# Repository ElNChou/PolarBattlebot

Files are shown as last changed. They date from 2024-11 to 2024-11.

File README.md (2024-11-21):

# PinguBot - 2024

### Historia del Battlebot
Los climas helados son muy castigadores. No solo por todas las dificultades que presenta sobrevivir a temperaturas extremas, si no que también por lo gente que aparece por estos lugares sin prepararse. Estas personas son lentamente consumidas por el frío insoportable hasta lo más profundo de su ser, haciéndoles perder el interés por la cosas y la bondad. Esto es algo que Pingu sabe muy bien, pues ha sido víctima de un acto de crueldad solo posible con alguien de frío corazón.

En uno de sus paseos rutinarios con su querida madre, Pingu se alejó demasiado y se perdió por la montaña helada en que se encontraban explorando, pero encontró a un humano extremadamente amable que lo encontró. Sin esperar nada a cambio, este humano lo llevó en brazos hasta llevarlo de vuelta con su admirada guardiana, pero justo antes de que pudieran darle las gracias, este individuo cambió completamente de parecer y arrojó a Pingu al acantilado, enfrente de su madre.

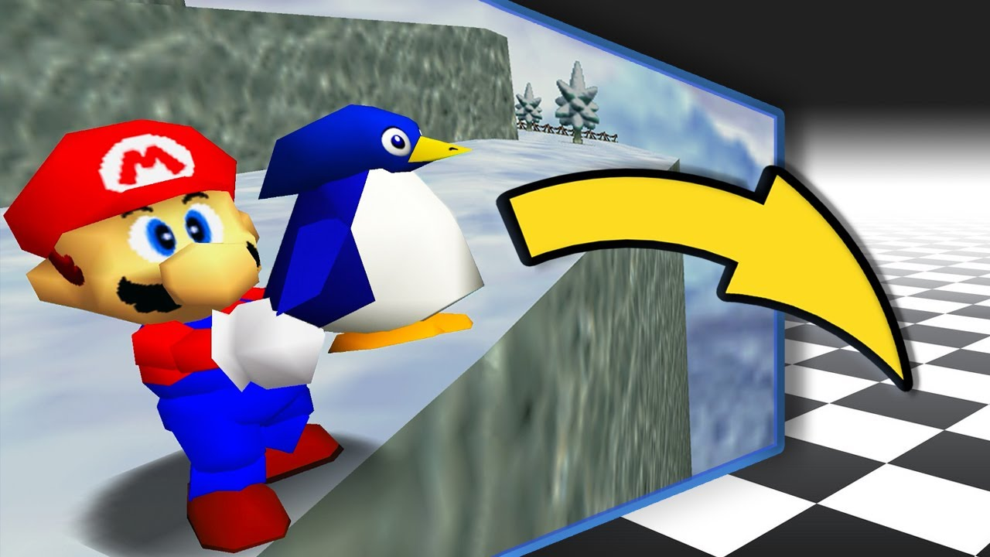
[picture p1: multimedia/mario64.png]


Tras este acto completamente repentino, Pingu cayó mientras escuchaba a lo lejos los ruidos que su furiosa madre hacía, desvaneciéndose lentamente... pero con una caída estratégica logró sobrevivir. Con esto aprendió a nunca más confiar en extraños, pues no se podía creer que alguien fuera capaz hacer algo así.
Tras este suceso, nuestra ave caída decidió nunca más salir de su iglú, y convertirlo en un tanque de guerra que lo protegiese, con el que se adentraría en la sociedad humana buscando a este malhechor.

Su extenuante búsqueda lo trajo a la competencia de battlebots, en donde pondrá a prueba sus habilidades y la resistencia de su querido transporte, con el que tantos viajes ha compartido.
  
¡Afiche del robot!
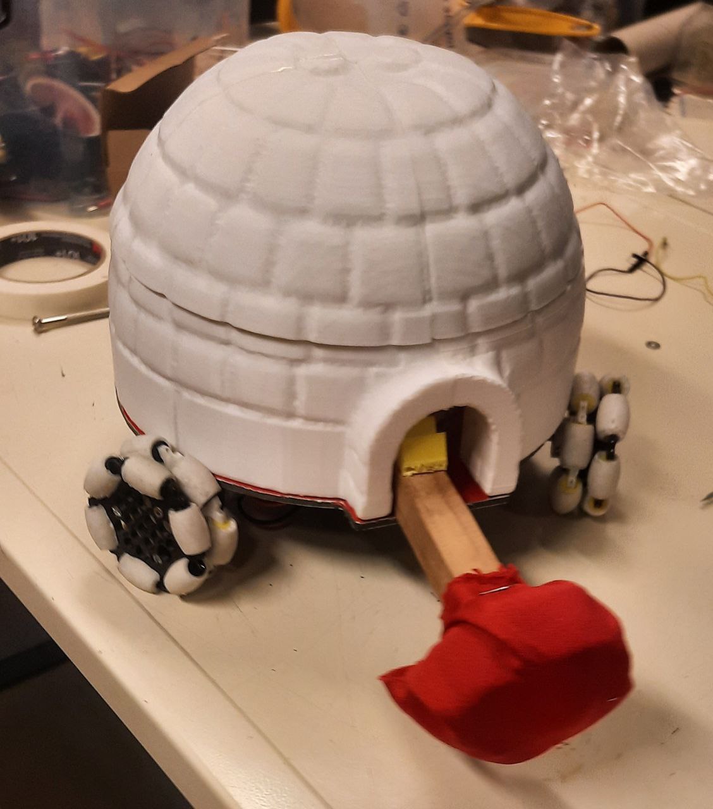
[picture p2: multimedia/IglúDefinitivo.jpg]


## Integrantes
- Camila Cáceres T. -  FCFM 
- Javier Ignacio Azócar -  FCFM 
- Tomás Rajevic P. -  FCFM 

## Descripción del proyecto
  El robot de batalla se comunica a través de wifi, tiene una coraza con forma de iglú y cuenta con 3 ruedas omnidireccionales que permiten un desplazamiento amplio sin necesidad de rotación, además de un arma de resorte que empuja a los rivales al soltarse. Las ruedas, coraza y partes internas del arma fueron impresas en 3D y la base fue procesada en una máquina CNC.
### Estrategia utilizada
  
#### Ofensiva
El arma es un palo que tiene espuma en la punta, unido a un resorte que acumula tensión y se suelta para realizar un empuje análogo a un guante de boxeo.
Debido a problemas técnicos con el motor que usaba para esto (¡resultó estar malo!), se cambió por un servomotor a último momento tal que solo moviera el arma para farmear puntos.

#### Defensiva
La defensa del robot viene dada por su corteza, ya que al ser una semi esfera dificulta recibir golpes directos pues se deflectan ligeramente al no golpearse contra una superficie plana. Además tiene un desplazamiento omnidireccional, el cual facilita aprovechar los ángulos de su coraza y esquivar ataques o reposicionarse sin necesidad de frenarse al rotar.

### Diagrama funcional
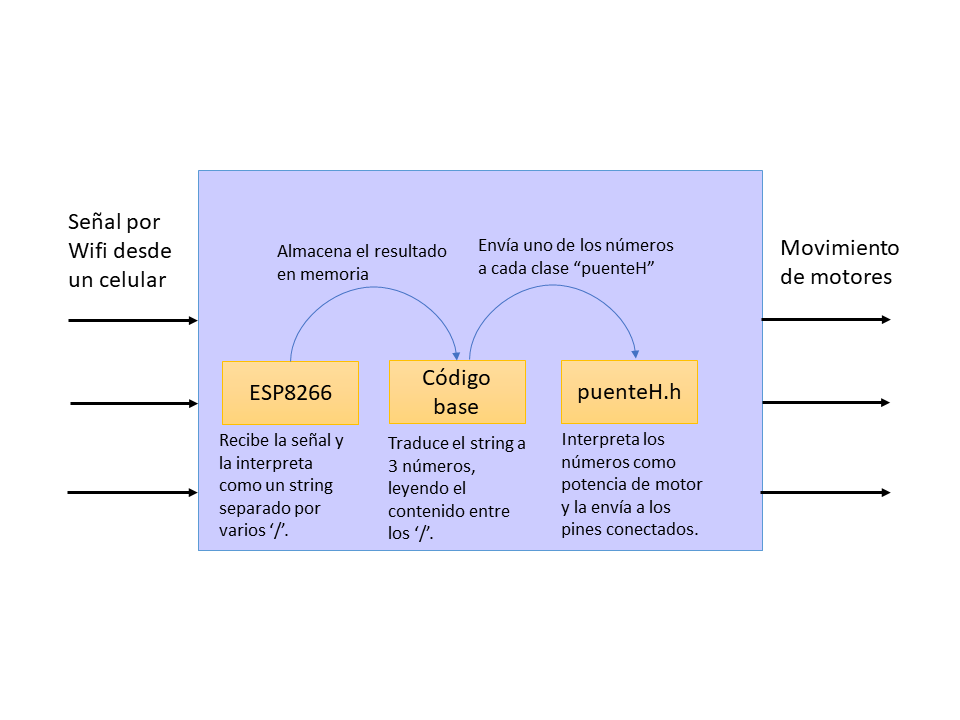
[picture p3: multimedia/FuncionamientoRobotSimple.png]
Robot Ejemplo


## Licencia
<br />Esta obra está bajo una <a rel="license" href="http://creativecommons.org/licenses/by-nc/4.0/">Licencia Creative Commons Atribución-NoComercial 4.0 Internacional</a>.

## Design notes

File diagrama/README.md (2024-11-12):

# Diagrama electromecánico

El arma es muy simple: Solo utiliza un pin digital para mover un motor hacia atrás, tensando así el resorte hasta que la rueda llega al final y se suelta, liberando un golpe sencillo y rápido, para luego volver a cargarse.

¿Pero cómo movemos el motor? No es suficiente con solo aplicarle el pin digital, por lo que compartirá un puenteH con la tercera omniwheel. La idea de esto es que aproveche la energía proporcionada por la batería, pues debe ser capaz de oponerse al resorte.

Para que esto se pueda hacer utilizando un solo pin, se cierra la parte del circuito donde normalmente iría el ENB, en el Pin1B se coloca el que queramos usar para activar el motor y Pin2B estará siempre cerrado, así que lo conectamos a a tierra sacrificando a la vez la flexibilidad de mover el motor en resera, pero para el arma no nos interesa. Gracias a eso, podemos controlar el motor aprovechando la pila de la batería sencillamente, utilizando un solo pin.

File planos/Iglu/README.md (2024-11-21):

# Modelo original que fue modificado
https://www.printables.com/model/204324-igloo-ornament

# MUY IMPORTANTE:
La base del iglú está mal medida y es posible que algunos agujeros no entren en caso de hacerlos con un taladro my pequeño. También es muy posible que si utilizas el arma en su forma predeterminada (un motor DC) debas cortarle algunas de las púas, están hecho más largos de lo normal pues es más fácil cortarlos que imprimir de nuevo.

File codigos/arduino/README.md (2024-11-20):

# Códigos Arduino
El código de este robot tiene dos archivos, el archivo 'puenteH' contiene una clase que nos permite mover un motor solo llamando a 'motor.move(valor)', el cual puede interpretar la dirección del movimiento a partir del signo del número que recibe. Polar.ino es el código principal que permite la conexión a la aplicación y requiere tener "puente.h" en la carpeta del proyecto..

Asegúrate que los pines coincidan con los del programa:

Si te posicionas en la misma dirección en la que mira el iglú, "Right" es el motor conectado a la derecha, "Left" a la izquierda, y "Tail" el que está por detrás (opuesto a la puerta). Los tres pines en cada uno de estos motores van en el orden de "OUT1,OUT2,ENA".

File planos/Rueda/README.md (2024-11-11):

# Molde
Archivos stl los cuales luego pueden ser usados para hacer un roller cubierto de caucho/silicona

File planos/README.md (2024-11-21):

# Archivos de planos incluidos

Aquí se encuentran todos los modelos utilizados para crear el battebot, además de algunos de referencia.

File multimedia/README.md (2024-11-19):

# Archivos multimedia de los battlebots

Se deben subir:
- Fotos de avance (en orden cronológico)

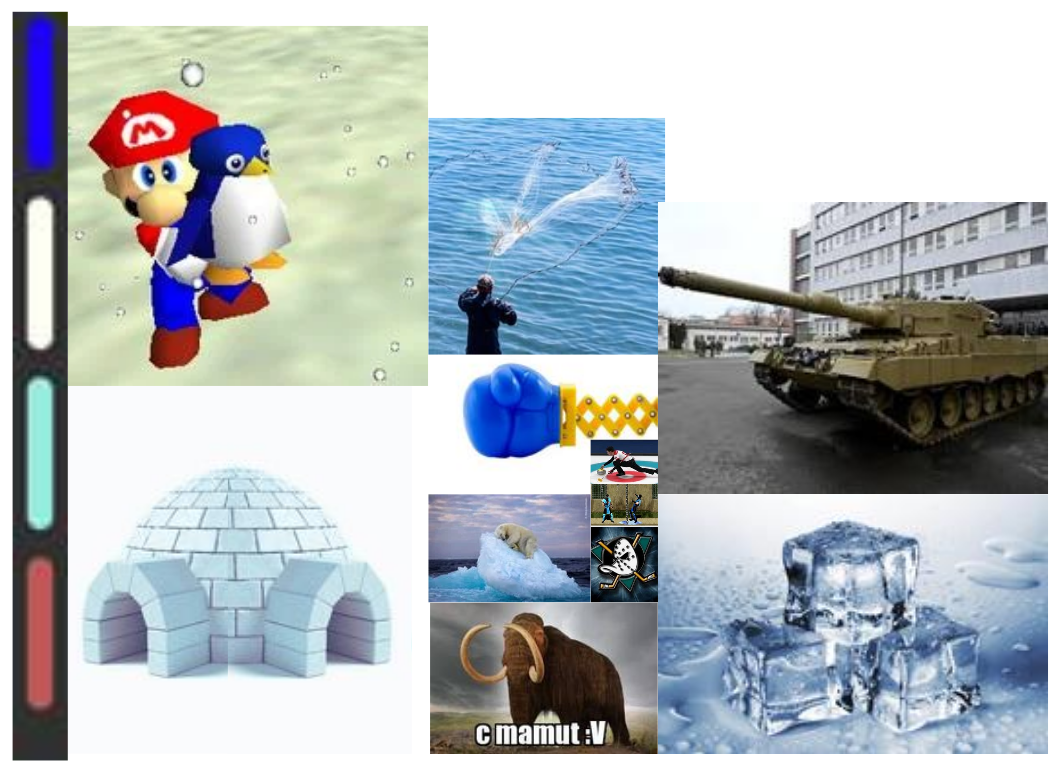
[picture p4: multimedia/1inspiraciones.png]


Imagen

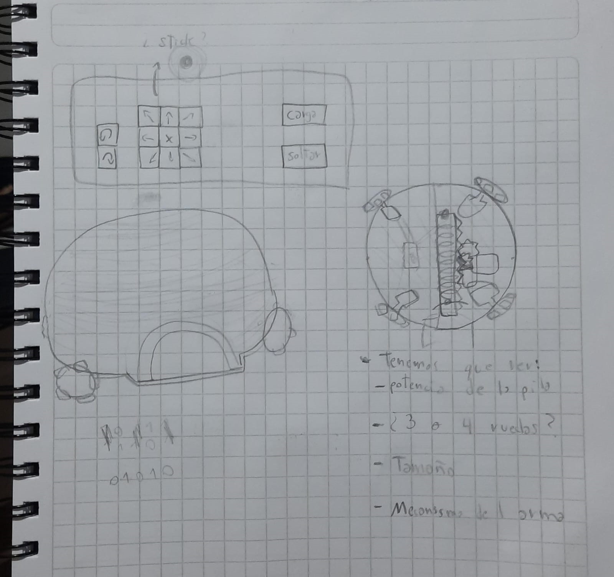
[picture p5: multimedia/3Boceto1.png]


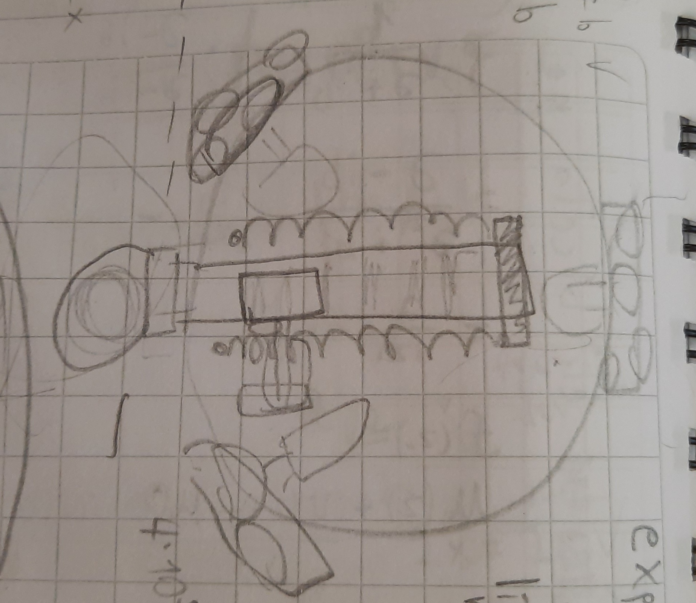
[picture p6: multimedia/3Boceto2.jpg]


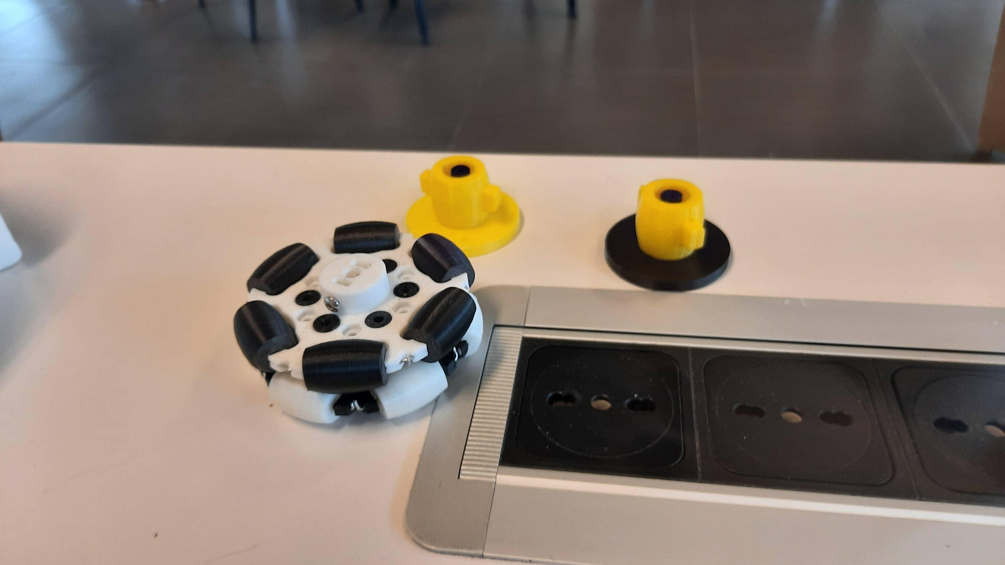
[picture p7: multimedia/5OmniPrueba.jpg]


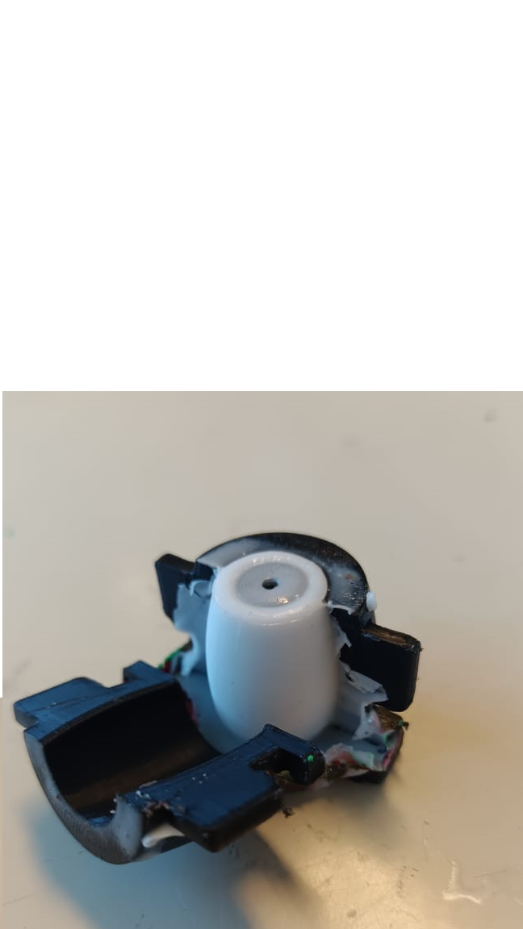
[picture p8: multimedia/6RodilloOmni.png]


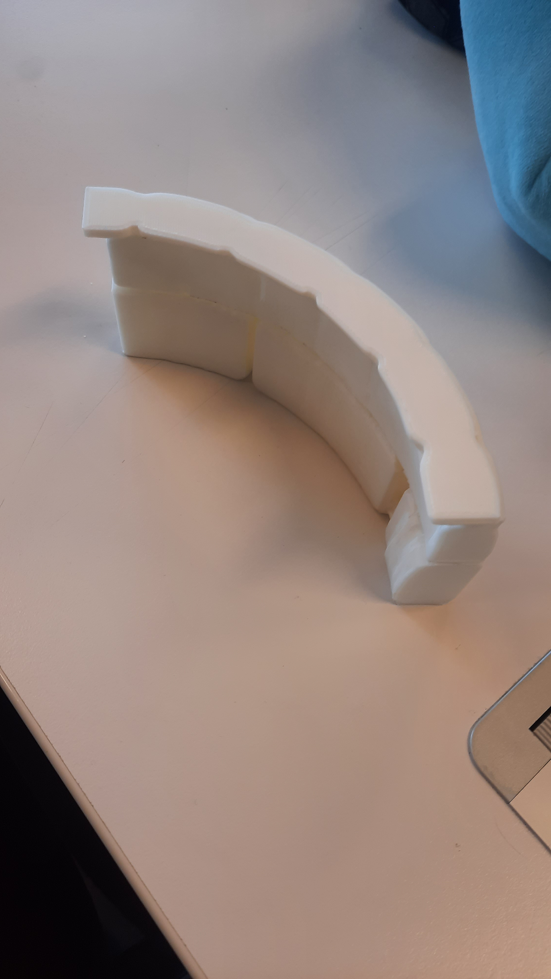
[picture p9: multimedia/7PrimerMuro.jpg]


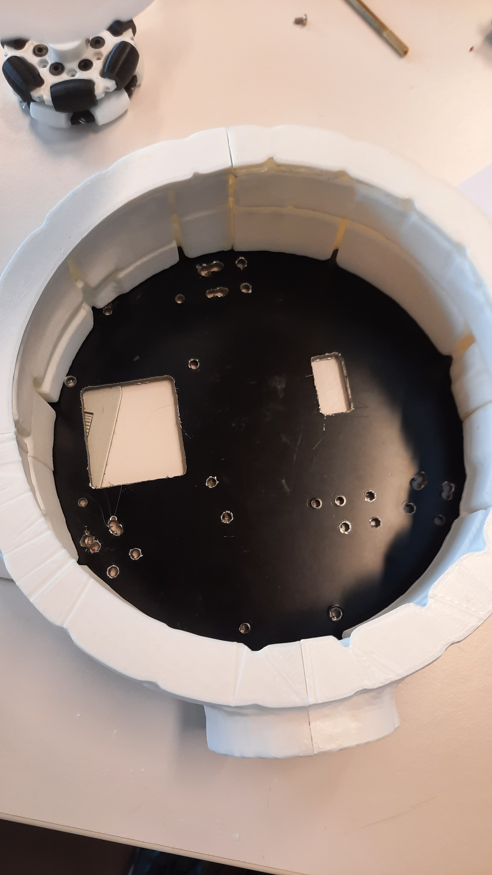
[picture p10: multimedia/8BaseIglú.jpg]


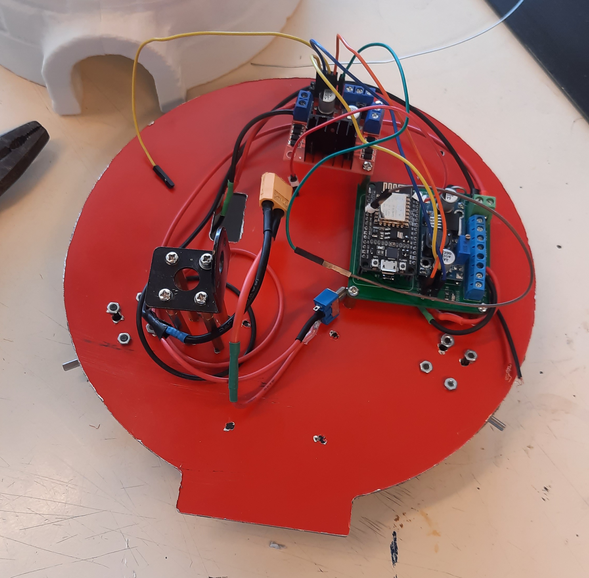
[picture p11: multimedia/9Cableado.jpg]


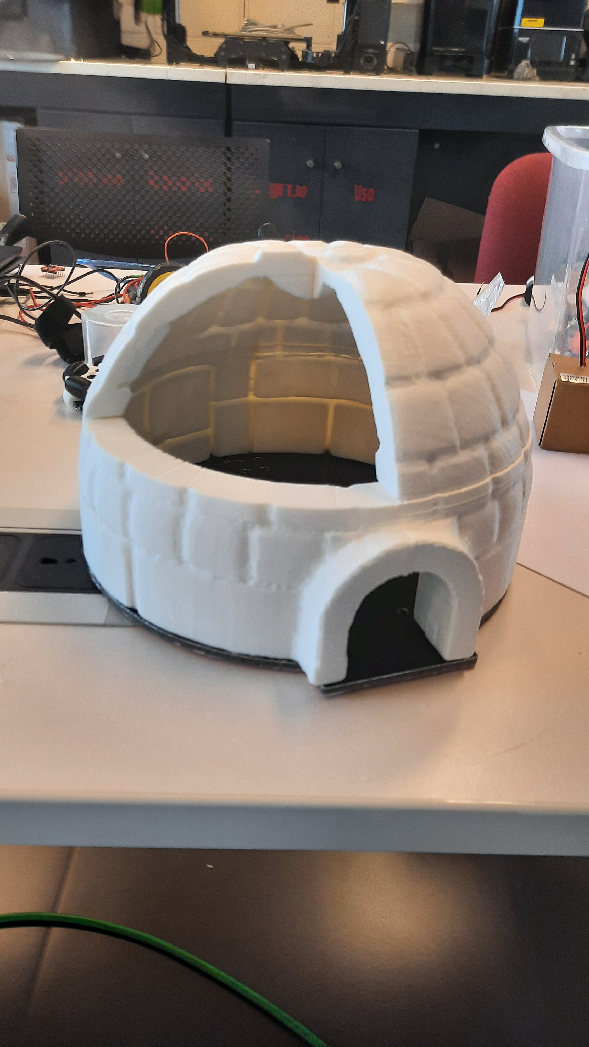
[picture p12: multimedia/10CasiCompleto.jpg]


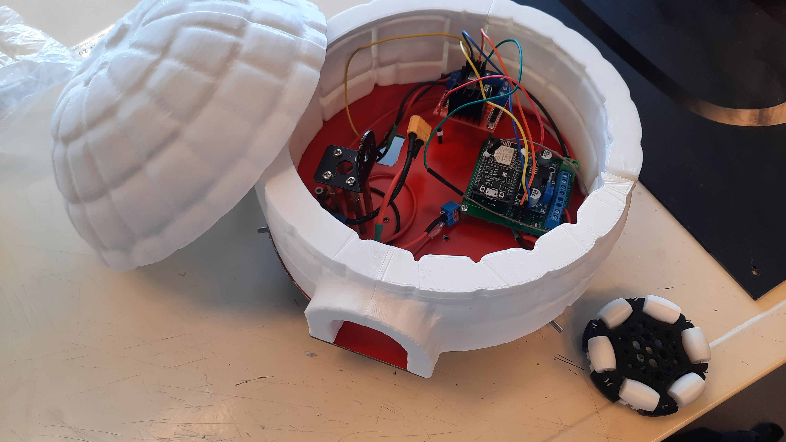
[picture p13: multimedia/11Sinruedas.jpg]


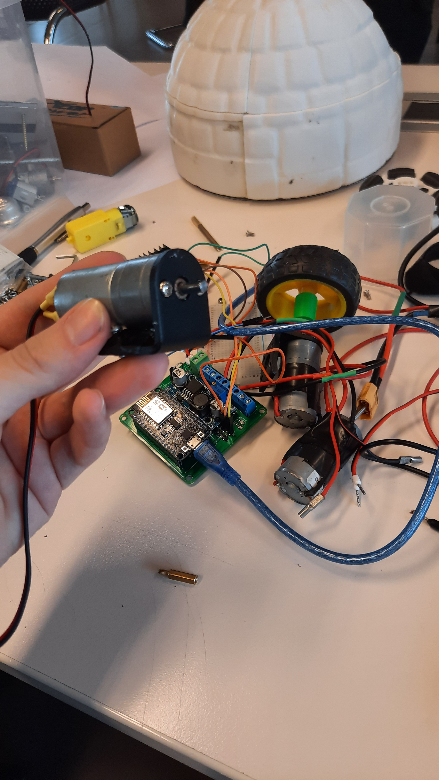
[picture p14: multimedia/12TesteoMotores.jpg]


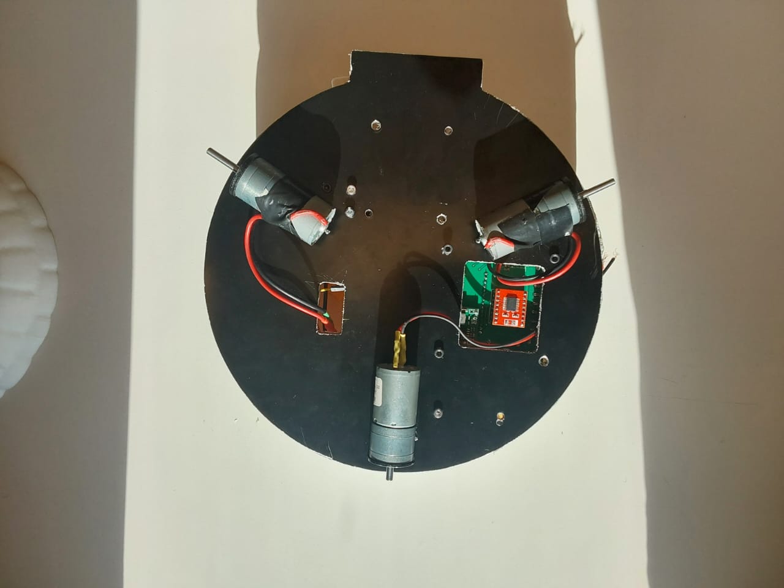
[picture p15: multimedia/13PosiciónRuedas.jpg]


Imagen

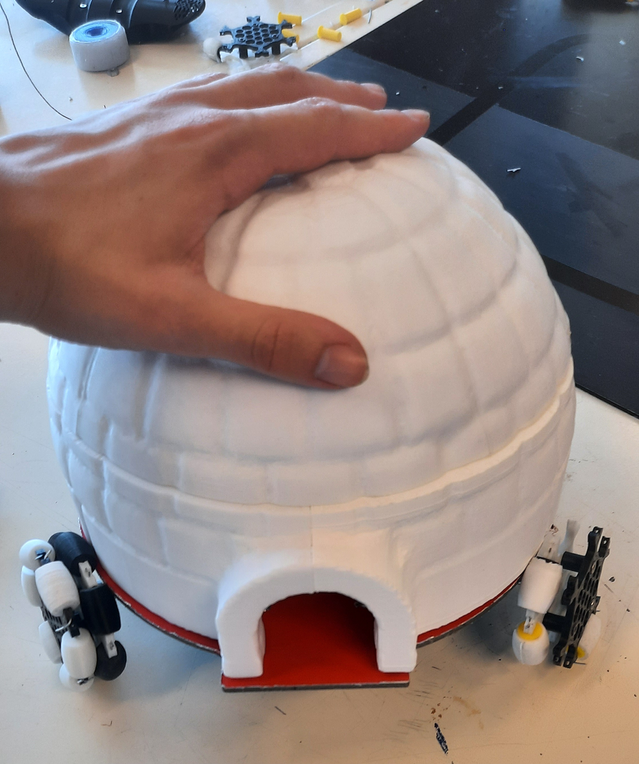
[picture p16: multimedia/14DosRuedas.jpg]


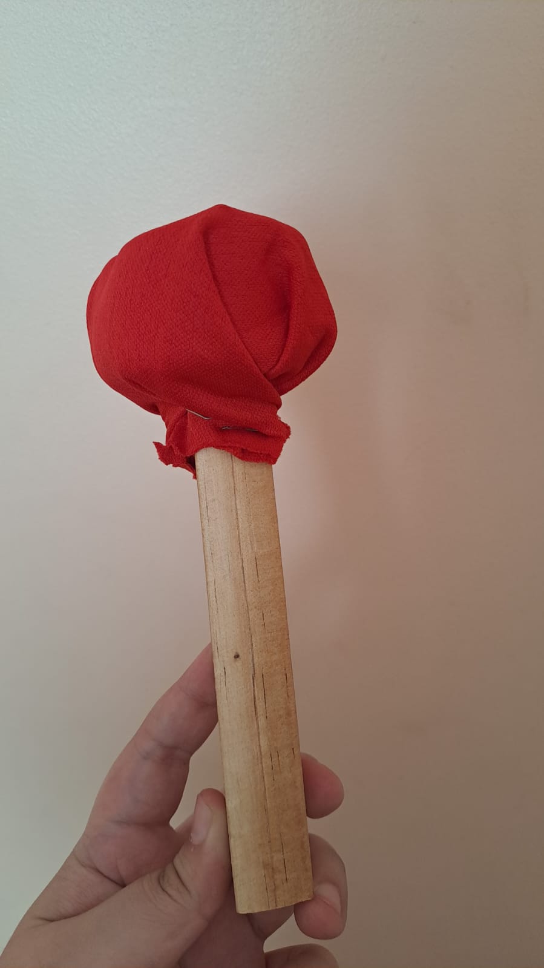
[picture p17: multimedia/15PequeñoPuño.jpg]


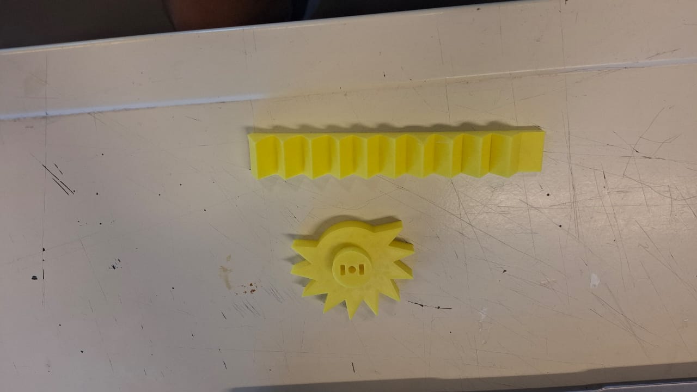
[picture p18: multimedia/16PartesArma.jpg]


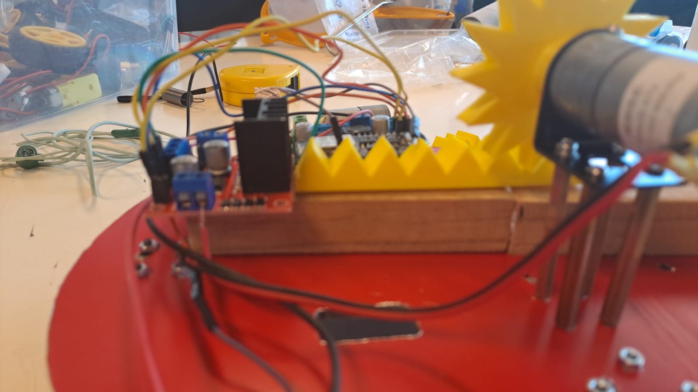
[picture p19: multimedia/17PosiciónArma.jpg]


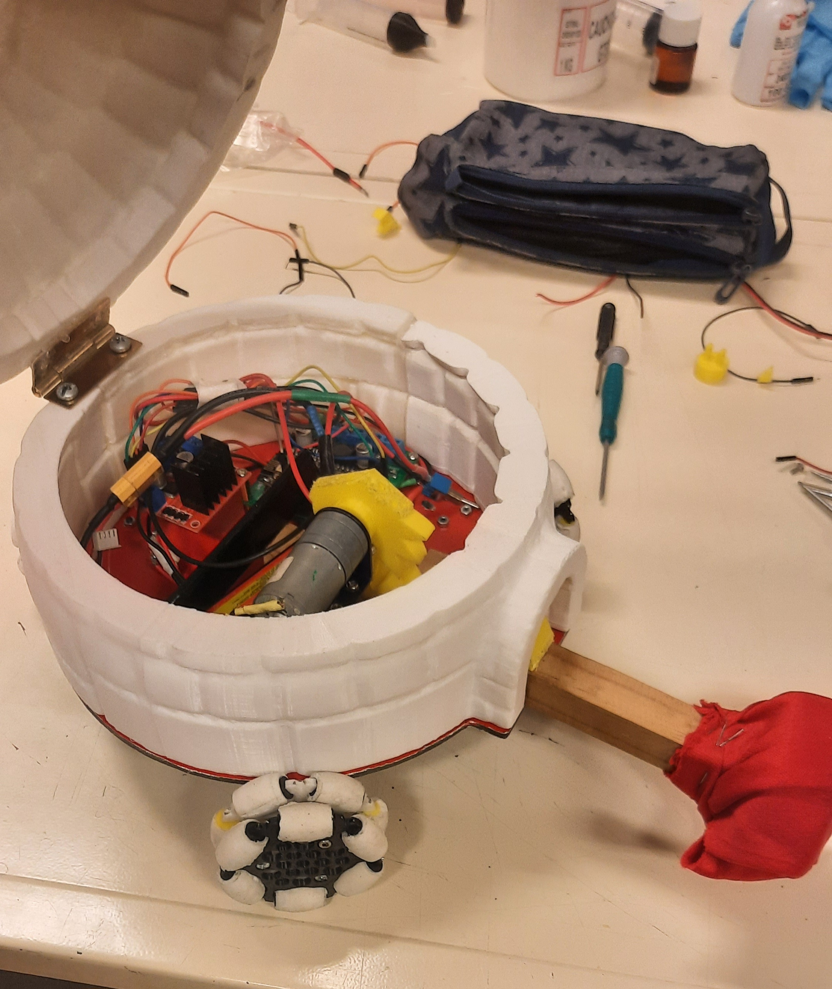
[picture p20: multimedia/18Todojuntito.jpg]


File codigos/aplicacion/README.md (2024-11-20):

# Código de la Aplicación

Aquí se encuentra la aplicación con la que se controla al robot.
Está el instalador apk, una foto del diagrama de bloques y el proyecto de appinventor aia

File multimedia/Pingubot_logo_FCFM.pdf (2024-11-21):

Equipo: Polar
Integrantes: Tomás Rájevic
Javier Azócar
Camila Cáceres
Curso: Módulo Interdisciplinario Battlebots | Nombre de Proyecto: PinguBot
| Descripción: Robot de batalla con ruedas omnidireccionales y un arma que dispara un golpe hacia delante. Está principalmente impreso en 3D, funciona con un ESP8266 y tiene forma de iglú
logos | Fecha: 12-11-2024

### Historia Había una vez, un pingüino que vivía en la cima de una montaña, de la cual fue lanzado al acantilado por un hombre muy malvado. Pingu pudo sobrevivir a la caída, pero desde ese día no confía en el resto, y convirtió su iglú en un tanque para siempre poder defenderse. Ahora, está buscando al

malhechor en la competencia.

El arma del iglú consiste en un puño el cual entra y sale por la entrada del iglú. este está conformado por el puño (círculo verde de la imagen), una rueda que al ponerla en un motor va a girar sobre el palo como un engranaje, esto estirará el resorte al que está unido y generará tensión, para que cuando la parte sin picos de la rueda llegue al palo, el puño pueda salir del iglú y golpear al rival.

La defensa del robot viene dada por su corteza, ya que al ser una semi esfera dificulta recibir golpes perpendiculares directos. Además tiene un desplazamiento omnidireccional, el cual facilita aprovechar los ángulos de su coraza y esquivar ataques o reposicionarse sin necesidad de rotar.

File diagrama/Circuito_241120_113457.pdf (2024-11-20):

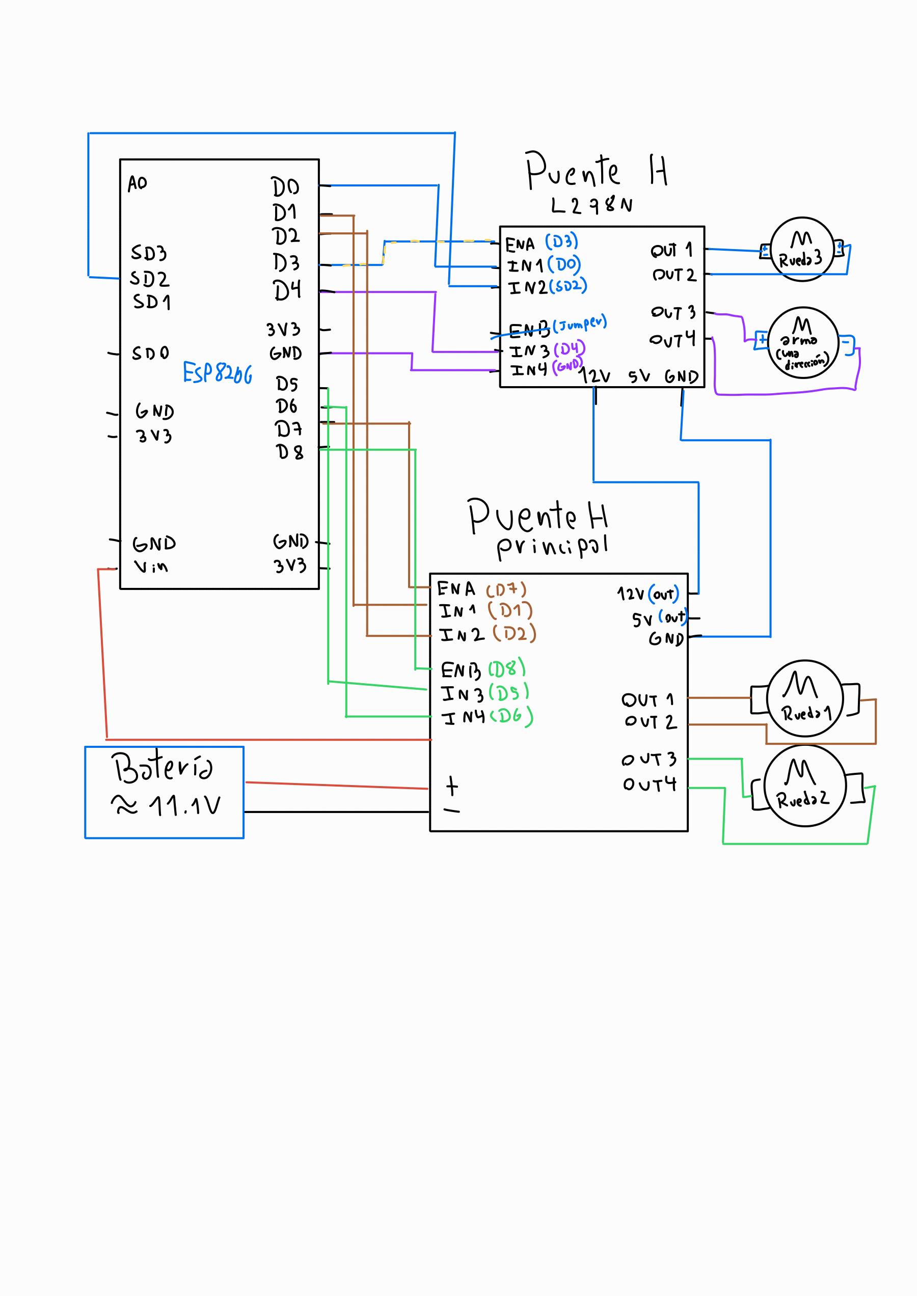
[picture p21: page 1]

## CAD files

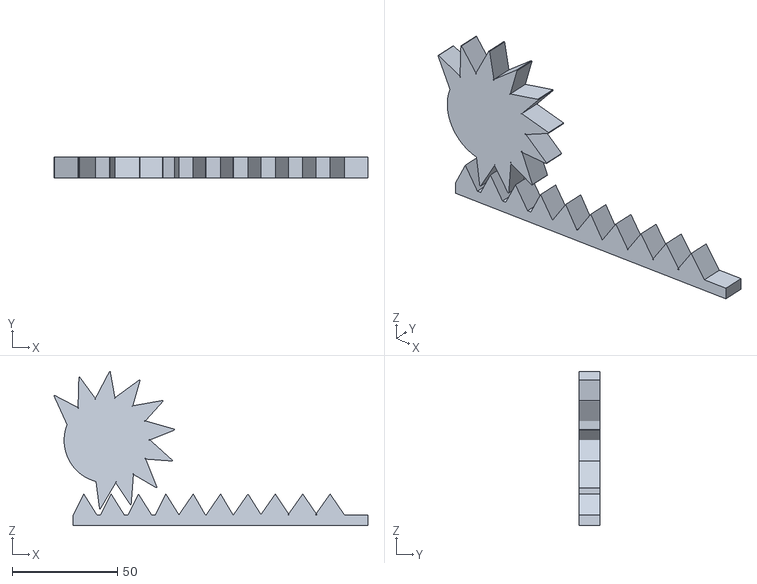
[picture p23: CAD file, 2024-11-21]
planos/Iglu/arma v1.stl
149.1 x 10.0 x 73.2

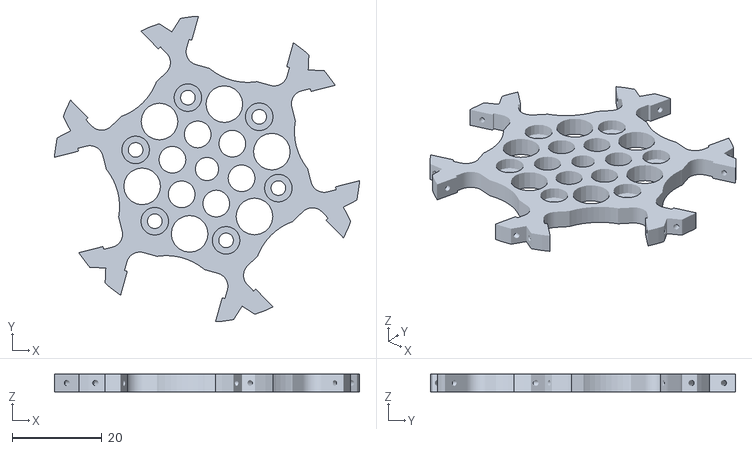
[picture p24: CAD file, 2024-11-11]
planos/Rueda/Original/omni_2.stl
68.1 x 68.2 x 4.00

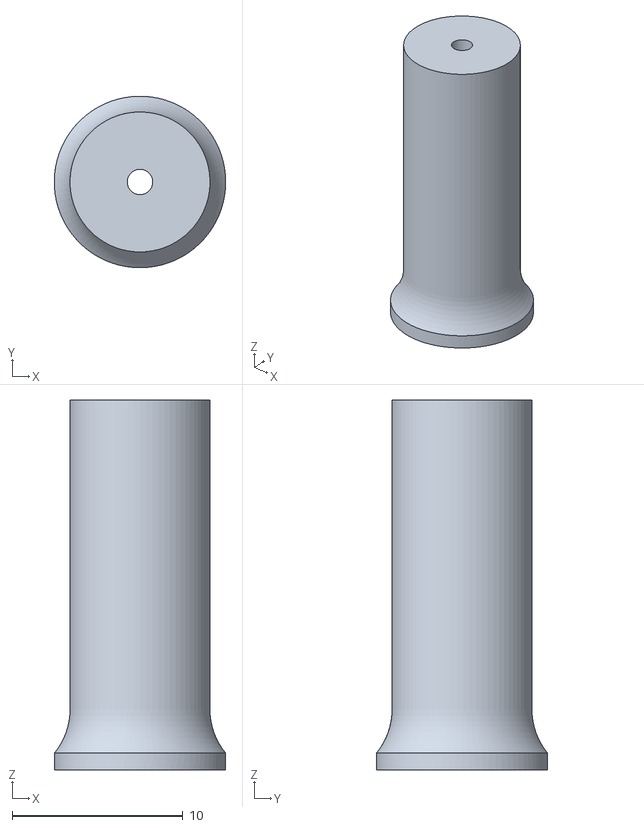
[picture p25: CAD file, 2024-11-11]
planos/Rueda/Roller.stl
10.0 x 10.0 x 21.7

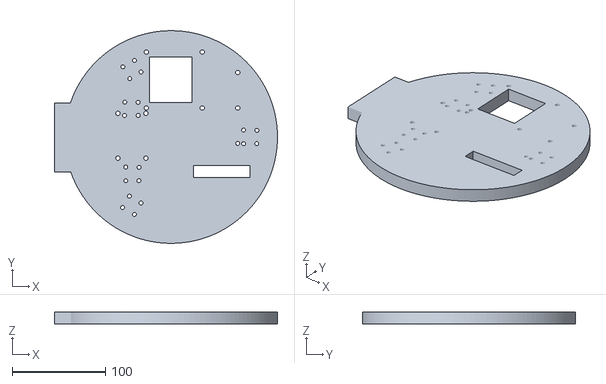
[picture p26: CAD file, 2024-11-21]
planos/Iglu/BaseIglú.stl
239.2 x 228.2 x 13.0

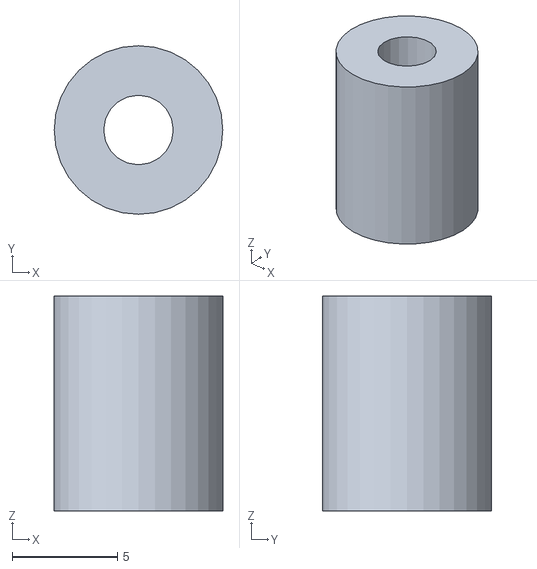
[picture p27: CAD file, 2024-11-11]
planos/Rueda/Original/omni_spacer.stl
8.00 x 8.00 x 10.2

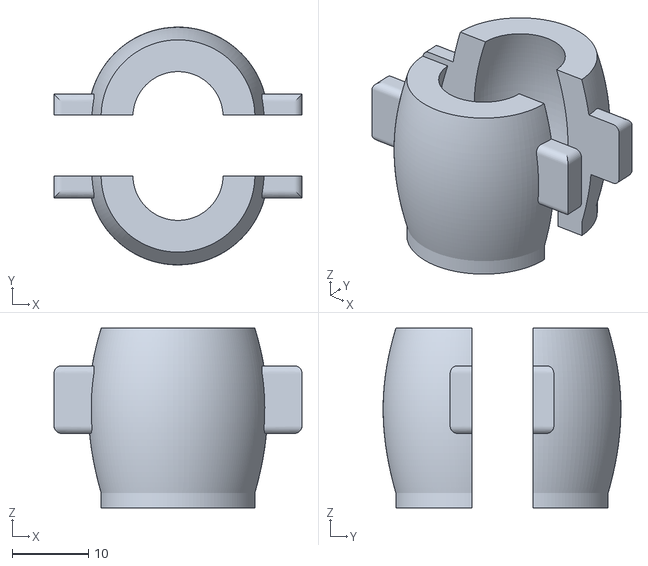
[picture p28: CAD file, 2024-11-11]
planos/Rueda/Parte superior molde.stl
32.5 x 31.2 x 23.5

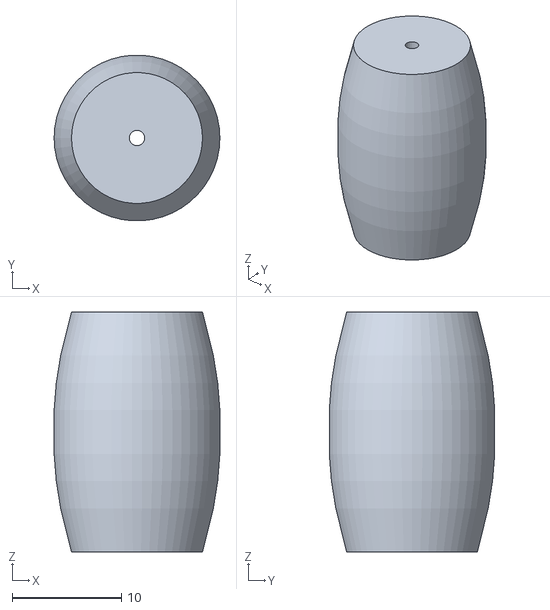
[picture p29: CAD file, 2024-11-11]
planos/Rueda/Original/omni_roller.stl
15.2 x 15.2 x 22.0

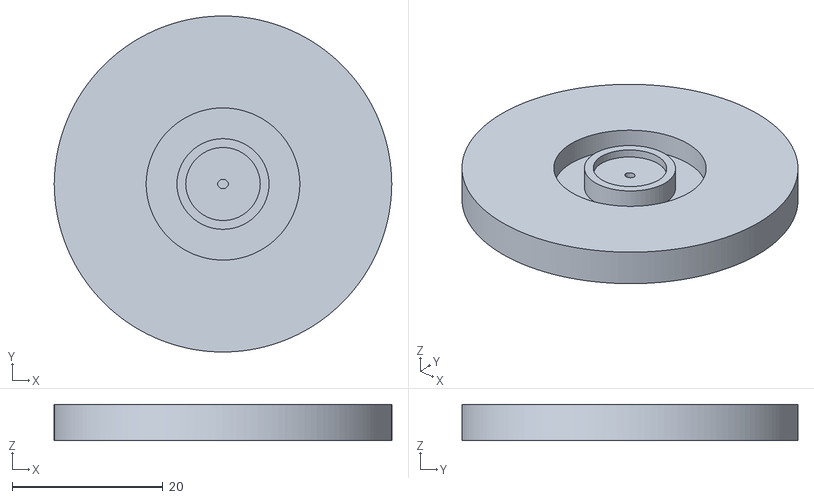
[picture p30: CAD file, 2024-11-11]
planos/Rueda/Parte inferior molde.stl
44.7 x 44.5 x 4.83

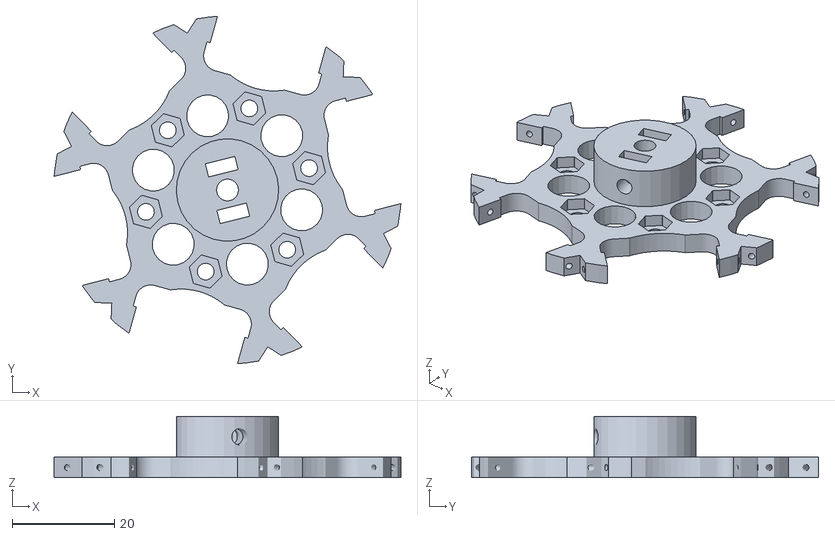
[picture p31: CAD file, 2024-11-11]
planos/Rueda/Original/omni_1_4mm_hole.stl
67.7 x 67.8 x 12.0

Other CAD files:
planos/Rueda/Original/omni_1_5mm_hole.stl

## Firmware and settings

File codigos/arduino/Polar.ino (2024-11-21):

//traducción de pines
//const int D0=16,D1=5,D2=4,D3=0,D4=2,D5=14,D6=12,D7=13,D8=15,RX=3,TX=1,SD3=10,SD2=9;
using namespace std;


//*******IMPORTANTE**********************************
//Cambia esta flag a "true" si estás usando un servo en vez de un motor DC.
//Esto lo implementamos porque nuestro motor estaba malo :( xd
bool usarServo=false;
//**************************************************

#include <ESP8266WiFi.h>
#include <Servo.h>
#include "puenteH.h"
const char* ssid = "PolarTesting";
const char* password = "elguantedeboxeo";

WiFiServer server(80);
//Esto es para detener el robot cuando no lo estemos usando
bool encendido=false;

//Inicializamos los 3 motores creando la una clase de "puenteH" para cada uno
//D5,D6,D8
puenteH Right(12,14,15);
//D2,D1,D7
puenteH Left(4,5,13);
//D0,SD2,D3
puenteH Tail(16,9,0);


//También declaramos el pin donde está el arma, D4
const int PinArma=2;
Servo arma;

//Y por último las variables donde guardaremos el input de la app
//Esto guardará la intensidad que deben tener los 3 motores en un momento dado
int joystick[3];


//https://www.servomagazine.com/magazine/article/get-rolling-with-omni-directional-wheels

void setup() {
  //Marcamos el arma como OUTPUT, los puenteH ya lo hacen por sí solos
  if(usarServo)arma.attach(PinArma);
  else pinMode(PinArma,OUTPUT);
  // Inicialización de WiFi
  WiFi.softAP(ssid, password);
  IPAddress IP = WiFi.softAPIP();
  server.begin();
}

void loop() {
  WiFiClient client = server.available();   // Espera a recibir un comando
  if (!client) {
    return;
  }

  while(!client.available()){delay(1);}
  
  //Lectura del comando, pero solo la parte que importa hasta el '/'
  String command = client.readStringUntil('/');
  command=client.readStringUntil('/');
  client.flush();

  //Chequeemos si estamos encendidos primero
  //Si NO estamos encendidos, nos encederemos en caso de recibir un 'E'
  if(!encendido){
    encendido=(command[0]=='E');
  
  //Si ya estamos encendidos, empezar la acción!!!
  }else{
    //Interpretaremos el comando guardado en 'command'
    switch (command[0]) {
     //M = Input de movimiento!!
     case 'M':
        //Leemos las nuevas intensidades para los motores que precalculó la aplicación muy amablemente
        for(int i=0;i<3;i++){
          command=client.readStringUntil('/');
          joystick[i]=command.toInt();
        }
        
        //Y actualizamos los motores
        //Se reciben en el orden: Right,Left,Tail
        Right.move(joystick[0]);
        Left.move(joystick[1]);
        Tail.move(joystick[2]);
        break;

      //A = INPUT DE ATAQUE!!!
      case 'A':
        if(usarServo)arma.write(0);
        else digitalWrite(PinArma,1);
        break;

      //S = input de detener ataque...
      case 'S':
        if(usarServo)arma.write(180);
        else digitalWrite(PinArma,0);
        break;

      //test servo
      case 'T':
        command=client.readStringUntil('/');
        arma.write(command.toInt());
        break;

      //X = volver a apagar (estado inicial)
      case 'X':  // Apagar
        if(usarServo)arma.write(0);
        else digitalWrite(PinArma,0);
        Right.move(0);
        Left.move(0);
        Tail.move(0);
        encendido=false;
        break;
    }
  }
  //Apagamos el cliente para eliminar los datos basura restantes
  client.stop();
}

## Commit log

2024-11-07 Update Polar.ino
    añadido el movimiento de los motores
2024-11-07 Cambio nombre de función de puenteH
    de mover -> move para consistencia con el código
2024-11-07 Update README.md
    Refleja lo que hay en la carpeta
2024-11-07 Aplicación actualizada
    Esta versión envía correctamente (por ahora) los valores de los motores
2024-11-11 Add files via upload
    https://www.thingiverse.com/thing:5027191#How%20I%20Designed%20This
    [omni_1_4mm_hole.stl, omni_1_5mm_hole.stl, omni_2.stl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]
2024-11-11 Rename Cascade.stl to Parte superior molde.stl
    [Parte superior molde.stl]
2024-11-11 Rename -0.1mm.stl to Parte inferior molde.stl
    [Parte inferior molde.stl]
2024-11-11 Delete planos/Iglu/gcode directory
    Los códigos de impresión 3D no son universales, así que es mejor solo dejar a disposición el iglú
2024-11-12 Create 4 Primera prueba motores y Wifi
2024-11-19 Rename 4 Primera prueba motores y Wifi to 4PruebaMotores (enlace)
2024-11-19 Rename Omniwheel de prueba.jpg to 5OmniPrueba.jpg
2024-11-19 Rename Mitad de Iglú y base.jpg to 8BaseIglú.jpg
2024-11-19 Rename Cableado sin iglú.jpg to 9Cableado.jpg
2024-11-19 Update and rename 4PruebaMotores (enlace) to Pruebas de motores
2024-11-20 Incluir "Modo servomotor" en Polar.ino
2024-11-21 Update Pruebas de motores
